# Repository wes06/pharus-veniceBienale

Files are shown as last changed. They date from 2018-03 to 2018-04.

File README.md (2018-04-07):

# pharus-veniceBiennale

Fan controller for interactive installation by Studio Pharus at Venice Biennale 2018.

## PCB

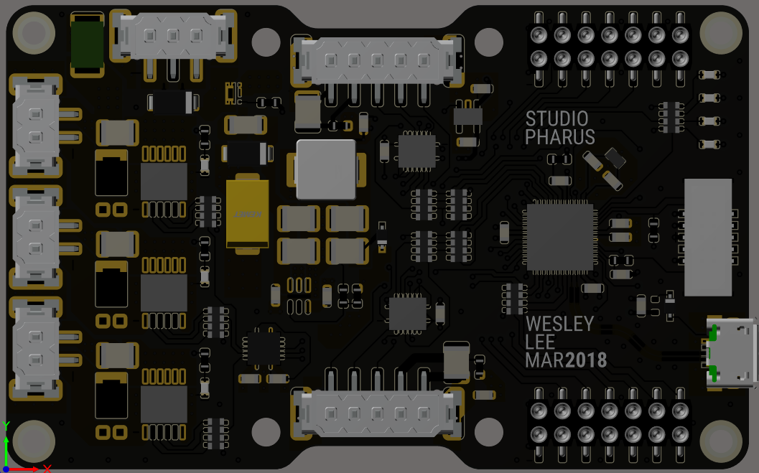
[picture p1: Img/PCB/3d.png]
3D visualization


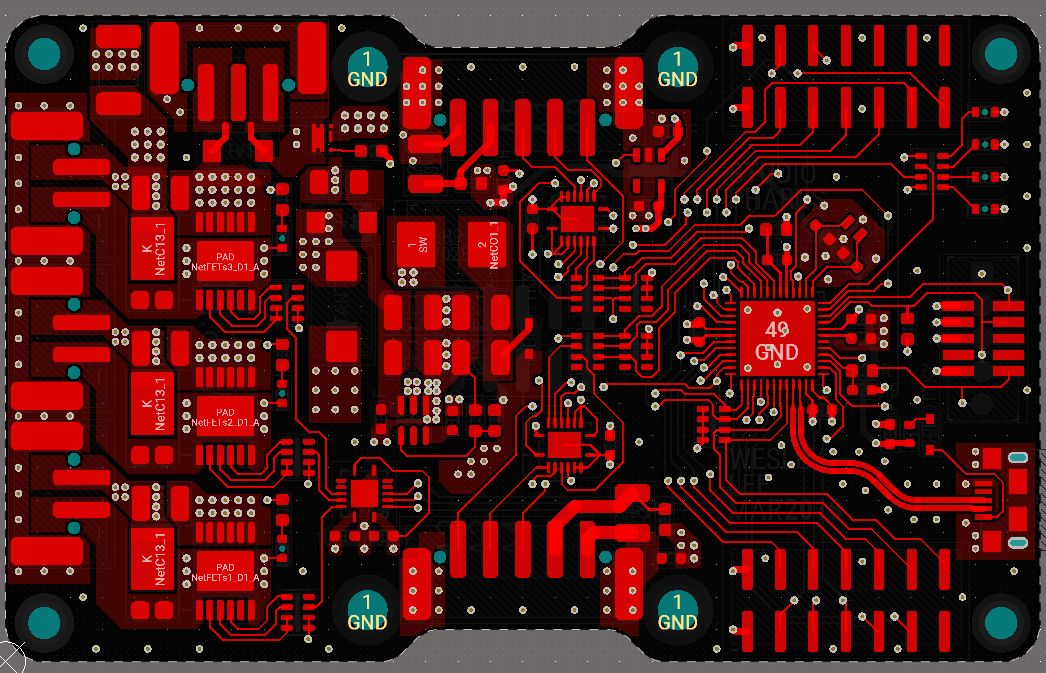
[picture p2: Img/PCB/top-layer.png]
PCB top layer


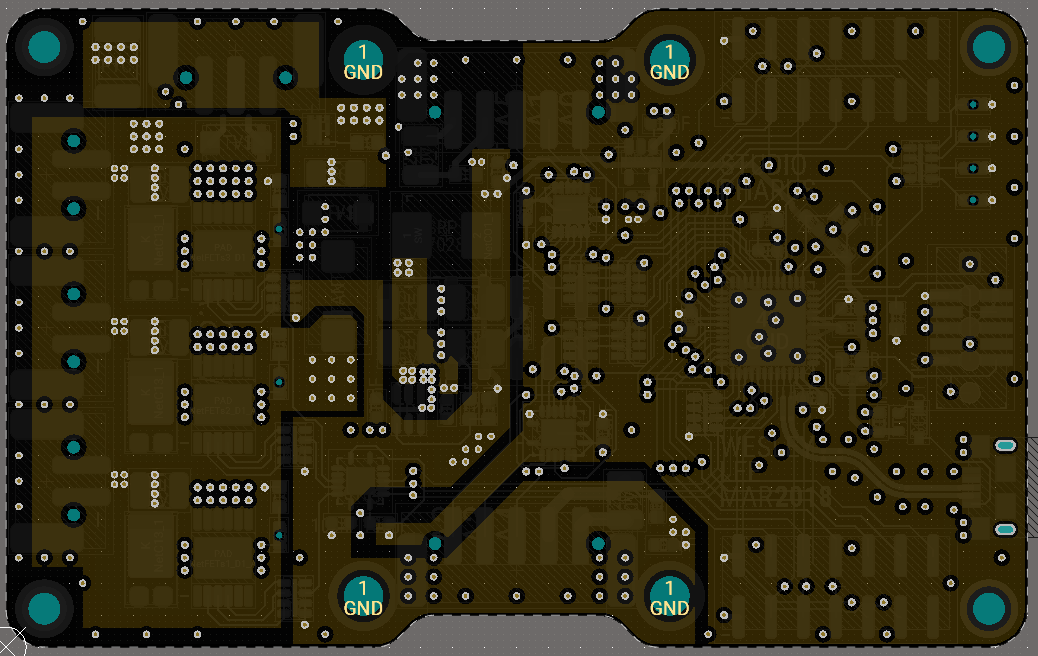
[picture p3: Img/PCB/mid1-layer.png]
PCB mid 1 layer


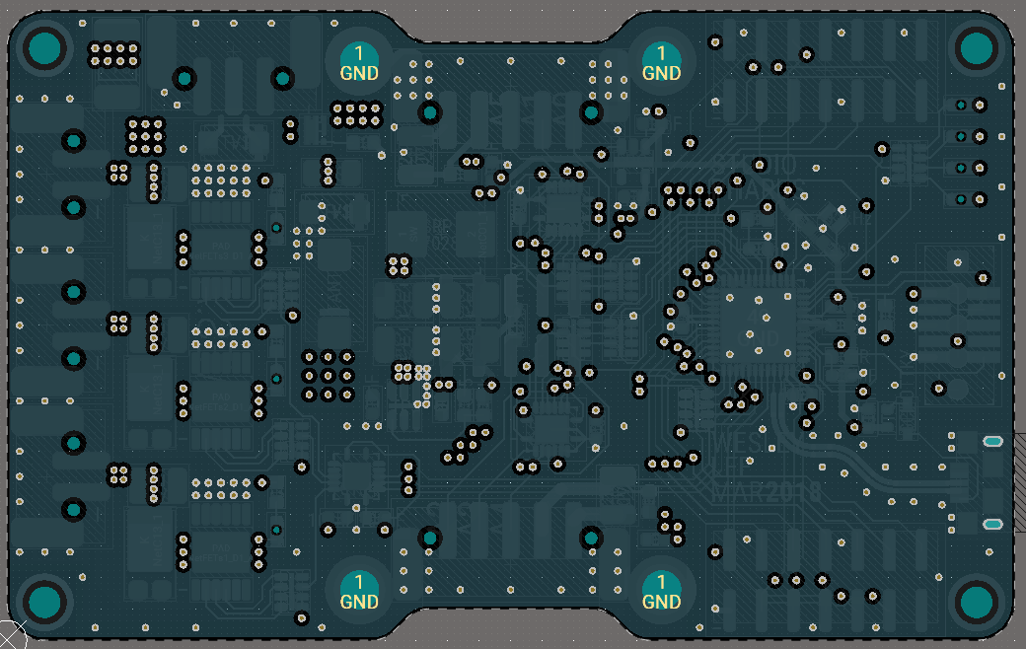
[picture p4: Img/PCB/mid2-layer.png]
PCB mid 2 layer


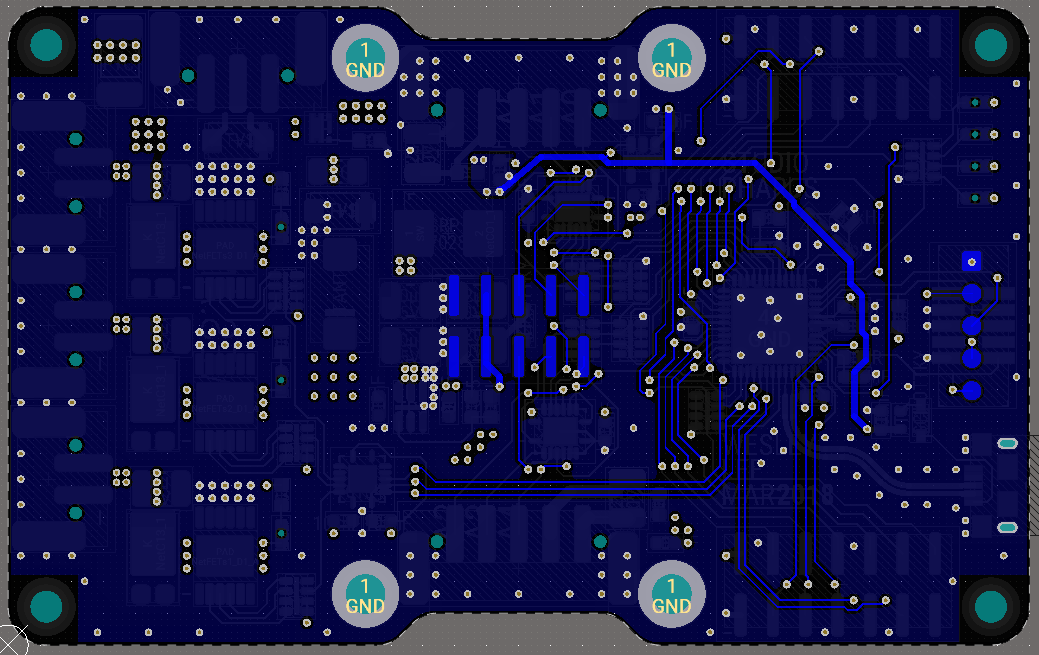
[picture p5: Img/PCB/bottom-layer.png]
PCB bottom layer


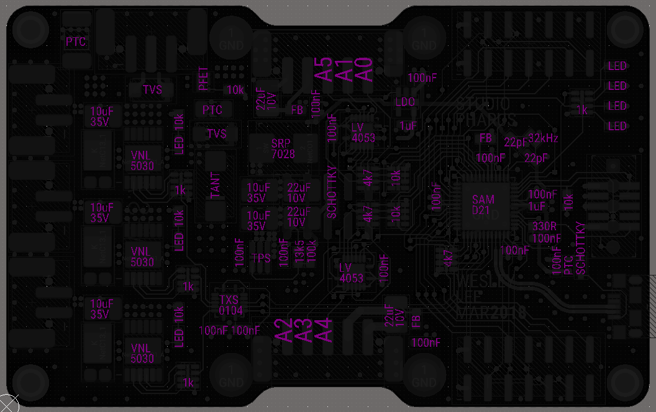
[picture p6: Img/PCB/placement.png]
Component placement


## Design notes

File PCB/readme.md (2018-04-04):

## To dos

 - Trocar a conexão da fonte do mux para 5V ao invés de 3.3V.
 - Lvl shifter para ABC do mux
 - colocar diodo da SMPS 5V depois do feedback
 - Trocar o fusivel da entrada Vin dos FETs por um P-FET contra polaridade reversa.

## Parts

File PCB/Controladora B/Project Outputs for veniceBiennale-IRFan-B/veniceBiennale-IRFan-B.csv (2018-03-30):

Comment | Description | Designator | Footprint | LibRef | Quantity
100nF | Capacitor MLCC | C1, C2, C3, C4, C7, C8, C10, C11, C15, C17, C18, C19, CBST1, CI3, CR | C0603_N | Capacitor | 15
1uF | Capacitor MLCC | C5 | C0603_N | Capacitor | 1
22uF | Capacitor MLCC | C6, C16 | C1210_N | Capacitor | 2
T598D157M016ATE065 | Polarized Cap | C13 | 2917 - Case D | Capacitor Polarized | 1
2uF | Capacitor MLCC | C14 | C0603_N | Capacitor | 1
10uF 35V | Capacitor MLCC | CI1, CI2, FETs1_C12, FETs2_C12, FETs3_C12 | C1210_N | Capacitor | 5
22uF 10V | Capacitor MLCC | CO1, CO2 | C1210_N | Capacitor | 2
22pF | Capacitor MLCC | CX1, CX2 | C0603_N | Capacitor | 2
824521121 |  | D2, D3 | DO214AC SMA | TVS, TVS Bidirectional | 2
Diode |  | D4, DU | SOD323F | Diode | 2
PTC | PTC, Resettable Fuse | F1 | C1206_N | PTC | 1
PTC | PTC, Resettable Fuse | F2 | 1812 | PTC | 1
Ferrite |  | FB1, FB5, FBA | R0603 | Resistor | 3
SBR5E60P5 |  | FETs1_D1, FETs2_D1, FETs3_D1 | PowerDI5 | Diode | 3
LED | LED | FETs1_L4, FETs2_L4, FETs3_L4 | LED 0603 Reverse | LED | 3
VNL5030J |  | FETs1_Q1, FETs2_Q1, FETs3_Q1 | PowerSSO-12 | VNL5030JTR | 3
1k |  | FETs1_R1, FETs2_R1, FETs3_R1, R4 | YC164 | Resistor Array - 4P | 4
10k |  | FETs1_R3, FETs2_R3, FETs3_R3, R5, R6 | R0603 | Resistor | 5
1778696 |  | FETs1_X1, FETs2_X1, FETs3_X1 | PTSM-2W-V-SMD | Connector 2W - TAB | 3
0ZCM0020FF2G | PTC, Resettable Fuse | FU | PTC0603 | PTC | 1
9774015243R 9774080243R |  | Hole1, Hole2, Hole3, Hole4 | Insert-Thread-SMD-M2 | Hole | 4
Hole |  | Hole5, Hole6, Hole7, Hole8 | M2.5 HOLE | Hole | 4
TPS54308 | Buck Converter | IC1 | SOT23 | TPS54308 | 1
SRP7028 |  | L1 | Inductor SRP7028 | Inductor | 1
TLMY1100-GS08 | LED | L5, L6, L7, L8 | LED 0603 Reverse | LED | 4
SIA483DJ-479954 |  | Q2 | SC70-6L | MOSFET P CH | 1
330R |  | R2 | R0603 | Resistor | 1
4k7 |  | R7, R9 | YC164 | Resistor Array - 4P | 2
10k |  | R8, R10 | YC164 | Resistor Array - 4P | 2
100k |  | RFB1 | R0603 | Resistor | 1
13k5 |  | RFB2 | R0603 | Resistor | 1
R I2C |  | RI1 | YC164 | Resistor Array - 4P | 1
20021521-00010T1LF |  | SWD1 | Header 10P 50mil | SWD | 1
DNP |  | SWD2 | SWD 5Pin SMD | SWD 5 Pin | 1
ATSAMD21G18 |  | U1 | QFN48_M | ATSAMD21G18 | 1
TXS0104E |  | U2 | QFN-14 | TXS0104E | 1
TPS70933 |  | U3 | SOT23-5_N | XC6222 | 1
SN74LV4053ARGYR |  | U4, U5 | QFN16 | SN74LV4053ARGYR | 2
USB Micro |  | USB | USB Micro | USB Micro | 1
Connector 5W - TAB |  | X2, X5 | PTSM-5W-V-SMD | Connector 5W - TAB | 2
LFXTAL050789 |  | X3 | Crystal 0805 | Crystal | 1
1778706 |  | X4 | PTSM-3W-V-SMD | Connector 3W - TAB | 1
Header 10Pos 5x2 |  | X6 | Header 5x2 SMD 2.54mm | Header 10Pos 5x2 | 1
Header 14Pos 7x2 |  | X9, X10 | Header 7x2 SMD 2.54mm | Header 14Pos 7x2 | 2

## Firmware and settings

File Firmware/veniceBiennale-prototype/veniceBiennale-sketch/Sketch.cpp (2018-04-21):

/*######################################################################

*/

#define LED1 8

#define FAN1_PIN 5    //connector by power input
#define FAN2_PIN 10   //connector in the center
#define FAN3_PIN 6    //connector far from power input

#define FAN1_DELAY 0
#define FAN2_DELAY 30
#define FAN3_DELAY 60

#define MUX_CONTROL 2 //ctrl pin for Analog Mux Switches (ABC)
#define MUX_CONTROL_DEFAULT LOW

#define IR_PIN1 A1  //
#define IR_PIN2 A5  //

#define DIST1_THRES 120
#define DIST2_THRES 400

#define STATE0_DEBOUNCE_LENGTH 1000
#define STATE1_DEBOUNCE_LENGTH 200




#define FAN1_INFHOLD_LENGTH 3000
#define FAN1_INFHOLD_INFLATEVAL 0
#define FAN1_INFHOLD_HOLDVAL 255
#define FAN1_INFHOLD_DELAY 0

#define FAN2_INFHOLD_LENGTH 3000
#define FAN2_INFHOLD_INFLATEVAL 0
#define FAN2_INFHOLD_HOLDVAL 120
#define FAN2_INFHOLD_DELAY 100

#define FAN3_INFHOLD_LENGTH 3000
#define FAN3_INFHOLD_INFLATEVAL 0
#define FAN3_INFHOLD_HOLDVAL 120
#define FAN3_INFHOLD_DELAY 200


#define FAN1_BREATHE_PERIOD 8000
#define FAN1_BREATHE_INFLATEVAL 255
#define FAN1_BREATHE_HOLDVAL 150
#define FAN1_BREATHE_DEFLATEVAL 0
#define FAN1_BREATHE_RESTARTVAL 120
#define FAN1_BREATHE_INFLATETIME 0.2
#define FAN1_BREATHE_HOLDTIME 0.5
#define FAN1_BREATHE_DEFLATETIME 0.1


#define FAN2_BREATHE_PERIOD 8000
#define FAN2_BREATHE_INFLATEVAL 200
#define FAN2_BREATHE_HOLDVAL 200
#define FAN2_BREATHE_DEFLATEVAL 0
#define FAN2_BREATHE_RESTARTVAL 120
#define FAN2_BREATHE_INFLATETIME 0.2
#define FAN2_BREATHE_HOLDTIME 0.2
#define FAN2_BREATHE_DEFLATETIME 0.5


#define FAN3_BREATHE_PERIOD 8000
#define FAN3_BREATHE_INFLATEVAL 255
#define FAN3_BREATHE_HOLDVAL 150
#define FAN3_BREATHE_DEFLATEVAL 0
#define FAN3_BREATHE_RESTARTVAL 150
#define FAN3_BREATHE_INFLATETIME 0.2
#define FAN3_BREATHE_HOLDTIME 0.4
#define FAN3_BREATHE_DEFLATETIME 0.3



//######################################################################

#include <Arduino.h>
#include "FanChannel.h"
#include "PCB_LED.h"
#include "IRIn.h"



// find out how to declare a class and initialize it later
PCB_LED fbLED1(LED1);
PCB_LED fbLED2(PIN_LED_RXL);
//PCB_LED fbLED1;

IRIn dist1(IR_PIN1,10);
IRIn dist2(IR_PIN2,10);

FanChannel fan1(FAN1_PIN, FAN1_DELAY);
FanChannel fan2(FAN2_PIN, FAN2_DELAY);
FanChannel fan3(FAN3_PIN, FAN3_DELAY);

boolean fan1inf = true;
bool fan2inf = true;
bool fan3inf = true;

//detectState vars
int state = 0;
bool state0Waiting = false;
unsigned long state0Millis;
bool state1Waiting = false;
unsigned long state1Millis;

bool holdStarted = false;


unsigned long lastInflated;


void detectStates(){
	//  volatile int dist2log = dist2.getAverage();
	//  volatile int dist1log = dist1.getAverage();
	//nothing detected
	if(dist1.getAverage() < DIST1_THRES)// && dist2.getAverage() < DIST2_THRES)
	{
		
		// keep inflated after 2secs of debounce
		if (!state0Waiting)
		{
			state0Millis = millis();
			state0Waiting = true;
		}
		else if(millis() - state0Millis > STATE0_DEBOUNCE_LENGTH){
			state = 0;
			// if it hasn't started inflating, reset the vars
			// if it started inflating, will not set fanXinf to true
			if(!holdStarted){
				fan1inf = true;
				fan2inf = true;
				fan3inf = true;
			}
		}
	}
	else
	{
		state0Waiting = false;
		holdStarted = false;
	} // end of nothing detected
	
	// something detected
	if(dist1.getAverage() >= DIST1_THRES)// || dist2.getAverage() >= DIST2_THRES)
	{
		
		// start breathing after 2 secs of debounce
		if (!state1Waiting)
		{
			state1Millis = millis();
			state1Waiting = true;
		}
		else if(millis() - state1Millis > STATE1_DEBOUNCE_LENGTH) state = 1;
	}
	else
	{
		state1Waiting = false;
	} // end of something detected
	
}

bool newBreath = true;

void switchStates(){
	switch (state)
	{
		case 1:
		SerialUSB.print("\tDeflating\t");
		fan1.deflate(0, 30);
		fan2.deflate(0, 30);
		fan3.deflate(0, 20);
		// 		if(millis() - lastInflated > 500){
		// 			fan1inf = true;
		// 			fan2inf = true;
		// 			fan3inf = true;
		// 		}
		// 		holdStarted = true;
		// 		if(fan1inf || fan3inf || fan2inf){
		// 			lastInflated = millis();
		// 			if(fan1inf) fan1inf = fan1.inflateAndHold(FAN1_INFHOLD_LENGTH, FAN1_INFHOLD_INFLATEVAL,FAN1_INFHOLD_HOLDVAL);
		// 			if(fan2inf) fan2inf = fan2.inflateAndHold(FAN2_INFHOLD_LENGTH, FAN2_INFHOLD_INFLATEVAL,FAN2_INFHOLD_HOLDVAL);
		// 			if(fan3inf) fan3inf = fan3.inflateAndHold(FAN3_INFHOLD_LENGTH, FAN3_INFHOLD_INFLATEVAL,FAN3_INFHOLD_HOLDVAL);
		// 		}
		newBreath = true;
		break;
		


		case 0:
		SerialUSB.print("\tBreathing\t");
		
		if(newBreath){
			newBreath = false;
			analogWrite(5, 255);
			analogWrite(10, 255);
			analogWrite(6, 255);
			delay(4000);
		}
		
		
		fan1.breathe2(25,20, 3500, 2700, 255, 0);
		fan2.breathe2(28,17, 3700, 2500, 255, 0); // esquerda
		fan3.breathe2(25,20, 3100, 3100, 255, 0);
		
		if(false){
			
			if(fan1.getBreathCount() > 100){
				fan1.setBreathCount(0);
			}
			if(fan2.getBreathCount() > 100){
				fan2.setBreathCount(0);
			}
			if(fan3.getBreathCount() > 100){
				fan3.setBreathCount(0);
			}
			
			fan1.breathe(
			FAN1_BREATHE_PERIOD,
			FAN1_BREATHE_INFLATEVAL,  FAN1_BREATHE_HOLDVAL, FAN1_BREATHE_DEFLATEVAL,  FAN1_BREATHE_RESTARTVAL,
			FAN1_BREATHE_INFLATETIME, FAN1_BREATHE_HOLDTIME,  FAN1_BREATHE_DEFLATETIME);

			fan2.breathe(
			FAN2_BREATHE_PERIOD,
			FAN2_BREATHE_INFLATEVAL,  FAN2_BREATHE_HOLDVAL, FAN2_BREATHE_DEFLATEVAL,  FAN2_BREATHE_RESTARTVAL,
			FAN2_BREATHE_INFLATETIME, FAN2_BREATHE_HOLDTIME,  FAN2_BREATHE_DEFLATETIME);
			
			fan3.breathe(
			FAN3_BREATHE_PERIOD,
			FAN3_BREATHE_INFLATEVAL,  FAN3_BREATHE_HOLDVAL, FAN3_BREATHE_DEFLATEVAL,  FAN3_BREATHE_RESTARTVAL,
			FAN3_BREATHE_INFLATETIME, FAN3_BREATHE_HOLDTIME,  FAN3_BREATHE_DEFLATETIME);
		}
		break;
	} // switch
}



void setup()
{
	SerialUSB.begin(250000);
	//pinMode(LED1, OUTPUT); pin is initialized in PCB_LED fbLED1
	pinMode(PIN_LED_RXL,OUTPUT);
	digitalWrite(PIN_LED_RXL,LOW);
	
	pinMode(PIN_LED_TXL,OUTPUT);
	digitalWrite(PIN_LED_TXL,LOW);
	
	
	// set MUX to point to connectors
	pinMode(MUX_CONTROL,OUTPUT);
	digitalWrite(MUX_CONTROL,MUX_CONTROL_DEFAULT);

	// some blinking to signal boot
	for(int i = 0; i < 5; i ++){
		analogWrite(LED1, 127);
		delay(100);
		analogWrite(LED1, 0);
		delay(100);
	}
	
	if(fan1inf || fan3inf || fan2inf){
		if(fan1inf) fan1inf = fan1.inflateAndHold(FAN1_INFHOLD_LENGTH, FAN1_INFHOLD_INFLATEVAL,FAN1_INFHOLD_HOLDVAL);
		if(fan2inf) fan2inf = fan2.inflateAndHold(FAN2_INFHOLD_LENGTH, FAN2_INFHOLD_INFLATEVAL,FAN2_INFHOLD_HOLDVAL);
		if(fan3inf) fan3inf = fan3.inflateAndHold(FAN3_INFHOLD_LENGTH, FAN3_INFHOLD_INFLATEVAL,FAN3_INFHOLD_HOLDVAL);
	}
	analogWrite(5, 255);
	analogWrite(10, 255);
	analogWrite(6, 255);
	delay(20000);
}

uint8_t i=0;

unsigned long lastPrint = 0;
void loop()
{
	
	if(millis() - lastPrint > 100){
		SerialUSB.print(millis());
		SerialUSB.print("\t");
		SerialUSB.print(state);
		SerialUSB.print("\t");
		SerialUSB.print(analogRead(A1));
		SerialUSB.print("\t");
		SerialUSB.println(dist1.getAverage());
	}
	// 	// 	delay(20);
	// 	//for(;;){
	// 	// heartBeats, aka the board is running
	// 	fbLED1.heartBeatAnalog(30,255,1,100);
	// 	if(state == 0) fbLED2.heartBeatDigital(500,0.5);
	// 	if(state == 1) fbLED2.heartBeatDigital(500,0);
	//
	// 	// add readings to the arrays
	dist1.addReading();
	// 	//dist2.addReading();
	//
	//
	//state = 0;
	// 	// use the readings to decide what to do
	detectStates();
	//
	// 	// does what was decided in detectStates()
	switchStates();


	
	
} // loop()

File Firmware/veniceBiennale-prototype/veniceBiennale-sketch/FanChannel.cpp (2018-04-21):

/*
* FanChannel.cpp
*
* Created: 3/20/2018 10:03:16 PM
* Author: wes
*/
#include <Arduino.h>
#include "FanChannel.h"

// default constructor
FanChannel::FanChannel(int _ctrlPin, int _fanDelay)
: controlPin(_ctrlPin), fanDelay(_fanDelay)
{
	pinMode(controlPin, OUTPUT);
} //FanChannel




// turns fan on with '_inflateValue' for '_period' time, then turns the fan on '_holdValue' permanently
// _delay is a delay on start up time, should not influence _period
bool FanChannel::inflateAndHold(int _period, int _inflateValue, int _holdValue)
{
	if (inflateAndHoldState == 0){
		inflateStartedMillis = millis();
		inflateAndHoldState = 1;
	}
	
	if(inflateAndHoldState == 1 && millis() - inflateStartedMillis >= fanDelay)
	{
		analogWrite(controlPin, _inflateValue);
		inflateAndHoldState = 2;
	}
	
	if(inflateAndHoldState == 2 && millis() - inflateStartedMillis > _period - fanDelay){
		analogWrite(controlPin, _holdValue);
		inflateAndHoldState = 3;
	}
	if(inflateAndHoldState == 3 && millis() - inflateStartedMillis > _period){
		inflateAndHoldState = 0;
		return false; // done inflating, now holding
	}
	return true;
}


void FanChannel::deflate(unsigned int _deflateVal, unsigned int _holdDeflateVal)
{
	

	if(deflateAndHoldState == 0 && !deflating){
		analogWrite(controlPin, _deflateVal);
		deflateStartedMillis = millis();
		deflateAndHoldState++;
		deflating = true;
		SerialUSB.print(" ");
		SerialUSB.print("deflateState0");
		SerialUSB.print(" ");
	}
	if(deflateAndHoldState == 1 && millis() - deflateStartedMillis > 15000)
	{
		analogWrite(controlPin, 250);
		deflateAndHoldState++;
		SerialUSB.print(" ");
		SerialUSB.print("deflateState1");
		SerialUSB.print(" ");
	}
	if(deflateAndHoldState == 2 && millis() - deflateStartedMillis > 15200)
	{
		analogWrite(controlPin, _holdDeflateVal);
		deflateAndHoldState = 0;
		SerialUSB.print(" ");
		SerialUSB.print("deflateState1");
		SerialUSB.print(" ");
		
	}
}


//Fan turns on and off
void FanChannel::breathe(
int _periodo,
int _inflateVal, int _holdVal, int _deflateVal, int _restartVal,
float _inflateTime, float _holdTime, float _deflateTime)
{
	int breathVal;
	if(breathingState == 0){
		breathingState++;
		breathStart = millis();
	}
	
	if(breathingState == 1 && millis() - breathStart >= fanDelay)
	{
		analogWrite(controlPin, _inflateVal);
		breathingState++;
	}
	
	if(breathingState == 2 && millis() - breathStart > static_cast< float >(_periodo)*_inflateTime)
	{
		analogWrite(controlPin, _holdVal);
		breathingState++;
	}
	
	if(breathingState == 3 &&  millis() - breathStart > static_cast< float >(_periodo)*(_inflateTime + _holdTime) - fanDelay)
	{
		analogWrite(controlPin,_deflateVal);
		breathingState++;
	}
	
	if(breathingState == 4 && millis() - breathStart > static_cast< float >(_periodo)*(_inflateTime + _holdTime + _deflateTime) + fanDelay)
	{
		analogWrite(controlPin,_restartVal);
		breathingState++;
	}
	
	if(breathingState == 5 && millis() - breathStart > _periodo)
	{
		breathingState= 0;
		this->setBreathCount(this->getBreathCount()+1);
	}
}



//Fan turns on and off
void FanChannel::breathe2(unsigned int rampUpStep, unsigned int rampDownStep, unsigned int highWait, unsigned int lowWait, unsigned int highVal, unsigned int lowVal)
{
	this->deflating = false;
	deflateAndHoldState = 0;
	SerialUSB.print(" ");
	SerialUSB.print(breatheVal);
	SerialUSB.print(" ");
	// pulse it at 100%
	if(rampState == 0){
		breathe2Start = millis();
		analogWrite(controlPin, 230);
		rampState++;
	}
	
	if(rampState == 1 && millis() - breathe2Start > 200)
	{
		rampState++;
	}
	
	if(rampState == 2)
	{//ramp up
		
		if(millis() - breathe2Start > rampUpStep){
			analogWrite(controlPin, breatheVal);
			breathe2Start = millis();
			
			breatheVal++;
		}
		if(breatheVal >= highVal) {
			rampState++;
			breathe2Start = millis();
		}
	}

	if(rampState == 3 && millis() - breathe2Start > highWait){
		rampState++;
	}
	
	if (rampState == 4){
		
		if(millis() - breathe2Start > rampDownStep){
			analogWrite(controlPin, breatheVal);
			breathe2Start = millis();
			breatheVal--;
		}
		if(breatheVal <= lowVal) {
			rampState++;
			breathe2Start = millis();
		}
	}
	
	if(rampState == 5 && millis() - breathe2Start > lowWait){
		rampState = 0;
	}

}






unsigned int FanChannel::getBreathCount(){
	return breathCount;
}

void FanChannel::setBreathCount(int _breathCount){
	breathCount = _breathCount;
}

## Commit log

2018-03-30 Stable proto firmware
    [arduino_zero.cfg]
2018-03-30 Finished (final?) PCB design
    [FETs.SchDoc, MCU.SchDoc, SMPS-3V.SchDoc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]
2018-03-30 To do list created for PCB files
2018-03-30 Conflicts created by Google Drive and backup folders removed
    [arduino_zero.cfg]
2018-04-03 FanChannel::rbeathe and other declarations corrected
    [FanChannel.cpp]
2018-04-04 Sample array size moved to #define
2018-04-04 Name corrected
    [veniceBiennale-IRFan-B.csv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]
2018-04-05 IR only version started
    [arduino_zero.cfg]
2018-04-07 IR and Doppler merged
    [arduino_zero.cfg]
2018-04-07 Excess dir removed
    [arduino_zero.cfg]
2018-04-07 Altium project structure updated
    [veniceBiennale-IRFan-B.PrjPCB]
2018-04-07 PCB screenshots added
2018-04-07 PCB image added to Readme
